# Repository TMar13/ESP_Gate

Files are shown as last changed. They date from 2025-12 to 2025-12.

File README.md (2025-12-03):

ESP Board for gate control

2 control relays (opening and partial opening)
2 24 V DC-AC  states - you can use 12V or other by adjusting R1 and R2 (10 mA optocoupler bias). It supports a dry contact imput on B3 (use 2 jumpers : see implantaion.jpg)
2 buttons for commands (opening and partial opening)
1 ESP 8266 for driving and home assistant interface

List of files:
- YAML code with two states, "open" and "closed": some gate provide the states "opening" and "closing": the code needs to be modified
- Component list and layout
- PCB files: PCB available at PCBway.fr at a competitive prices
- Electronic schematic (ignore component part numbers)
- STL Box
- Gate states flowchart

Carte de pilotage de portail à base d'ESP8266

2 relais de contrôle pour ouverture et ouverture partielle
2 états 24 V DC-AV - s'adapte à une autre tension en ajustant R1 et R2 (10 mA de polarisation de l'optocoupleur). Une entrée à contact sec est supportée sur B3 (utiliser 2 jumpers) : voir implantation.jpg
2 boutons de commande pour ouverture et ouverture partielle
1 ESP 8266 de pilotage

Liste des fichiers :
- code YAML avec 2 états "ouvert" et "fermé" : certains portails fournissent les états ouverture et fermeture : le code est à modifier
- liste des composants et implantation
- fichiers PCB : vous pouvez vous fournir chez PCBway.fr à tarif intéressant
- fichier STL pour boite
- schéma électronique (ne pas tenir compte des références des composants)
- logigramme des états du prtail

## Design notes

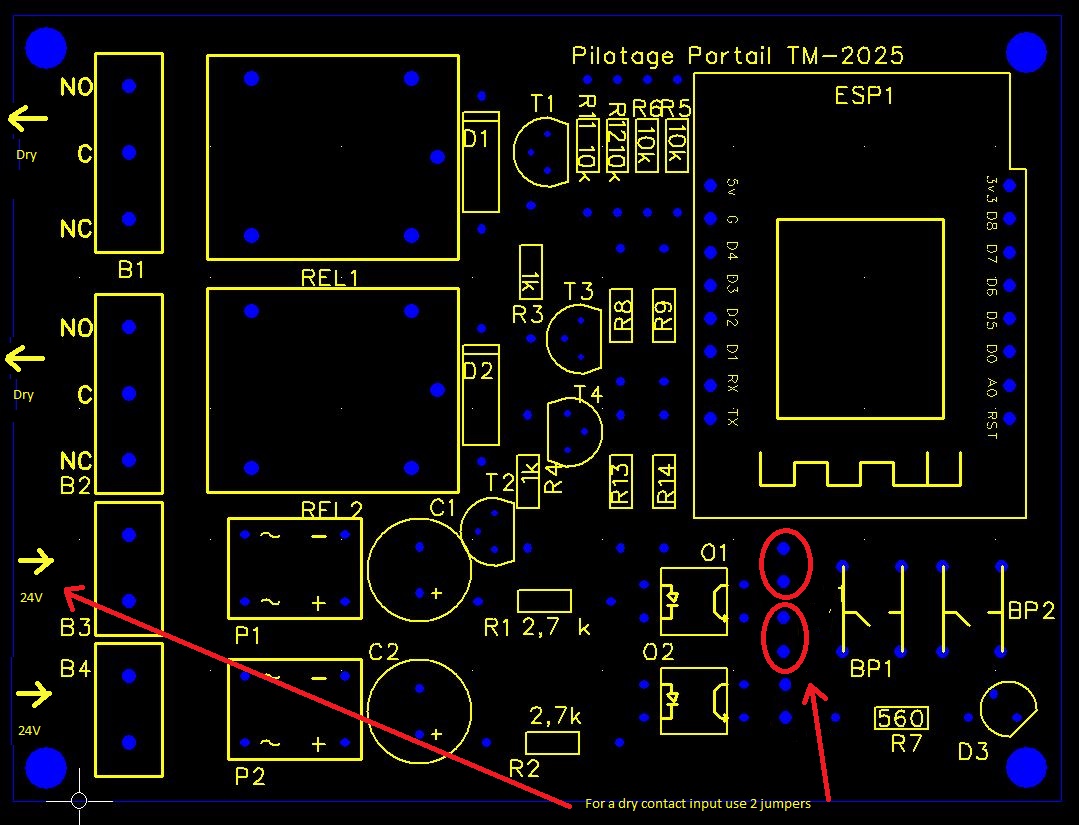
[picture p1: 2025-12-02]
implantation.JPG

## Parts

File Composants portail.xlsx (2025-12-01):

Désignation | Référence
D1,D2 | 1N4148
T1,T2 | T 58550 PNP
T3,T4 | 2N3904 NPN
ESP1 | ESP8266
R1,R2 | 2,7 kΩ
R3,R4 | 1 kΩ
R5,R6,R11,R12 | 10 kΩ
R7 | 560 Ω
R8,R9,R13,R14 | 1 kΩ
O1,O2 | Optocoupleur PC812C
P1,P2 | Pont redresseur DB207 DIP4 1000V
C1,C2 | 10 µF chimiQUE
D3 | Led 5 ou 3 mm
REL1,REL2 | Rel 5V - SRD-05VDC-SL-C
B3,B4 | Bornes doubles KF129 5,08mm
BP1, BP2 | Mini switch
B1,B21 | Bornes triples KF129 5,08mm

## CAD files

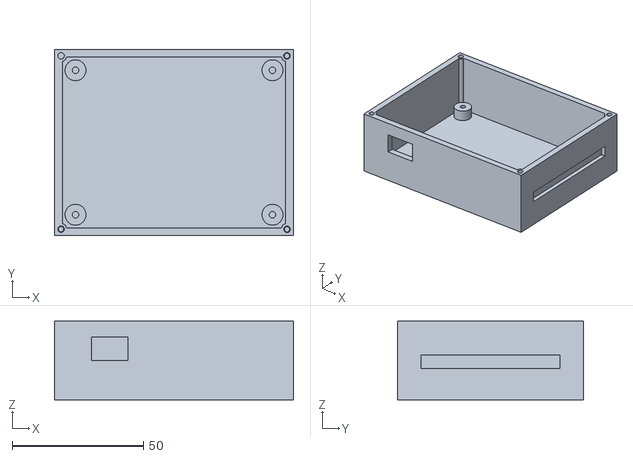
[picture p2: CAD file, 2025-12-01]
BoitePortail80x60.stl
91.0 x 71.0 x 30.0

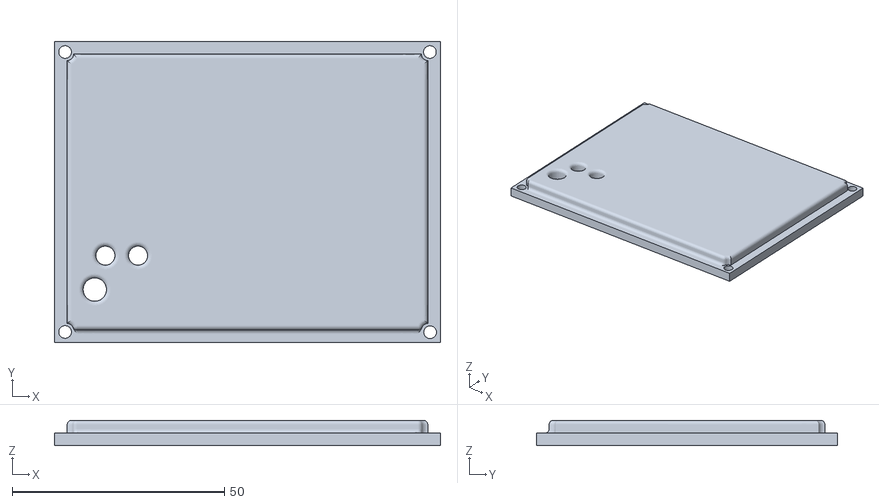
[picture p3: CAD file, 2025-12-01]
PortailCouv80x60.stl
91.0 x 71.0 x 6.00

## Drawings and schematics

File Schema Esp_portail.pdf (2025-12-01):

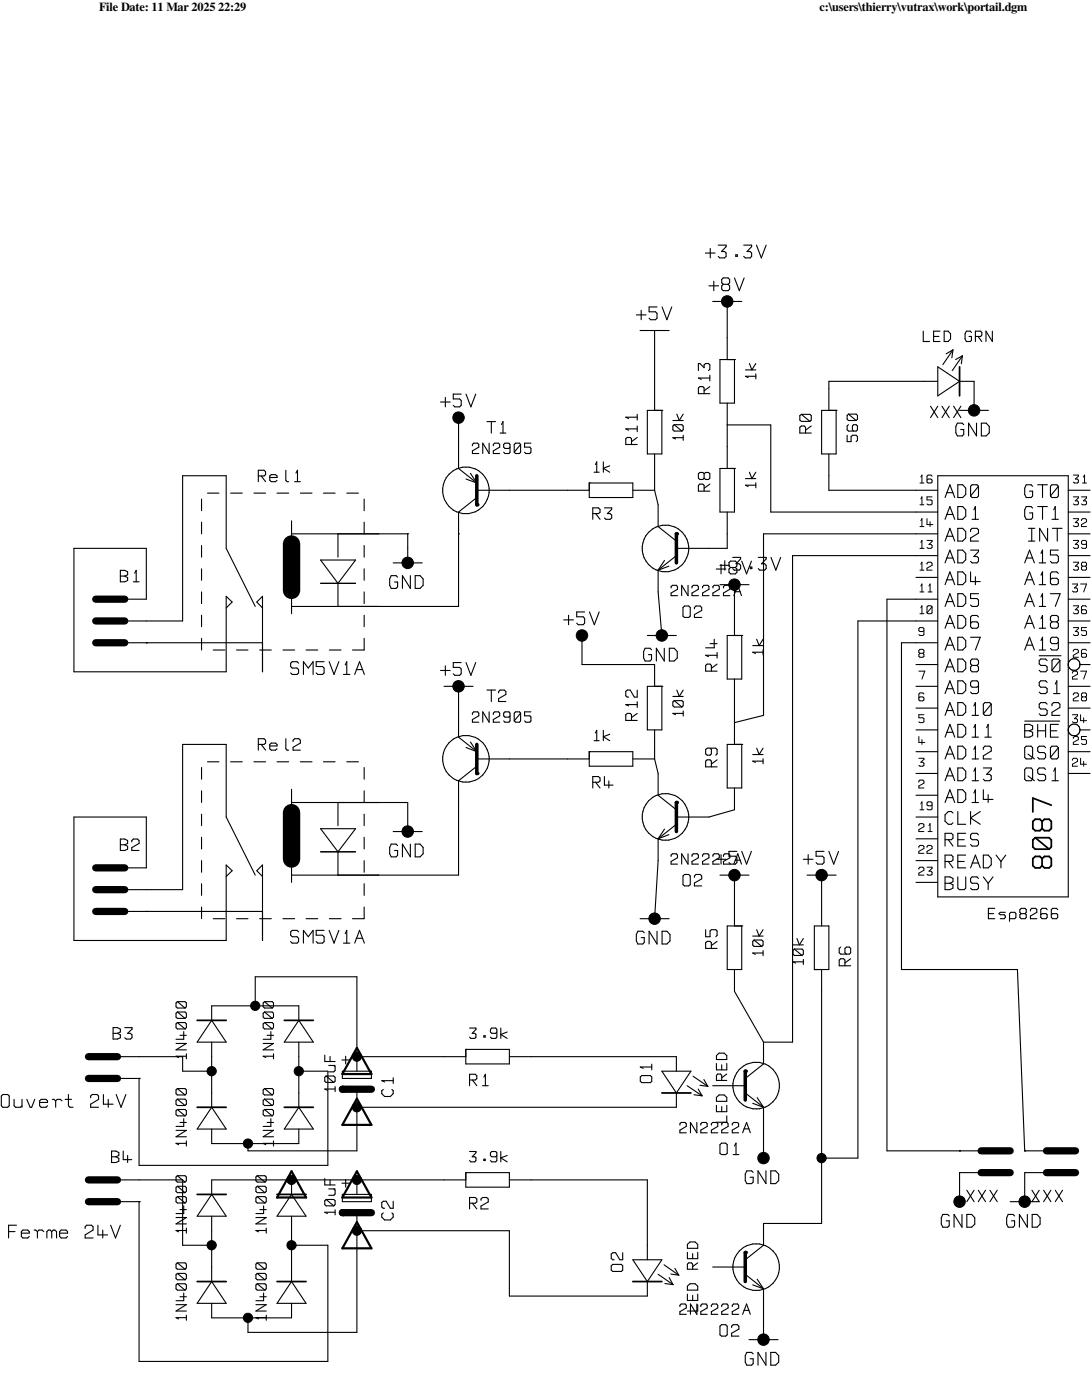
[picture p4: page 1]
File Date: 11 Mar 2025 22:29; c:\users\thierry\vutrax\work\portail.dgm

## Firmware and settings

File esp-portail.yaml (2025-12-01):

esphome:
  name: esp-portail
  friendly_name: Esp_Portail

esp8266:
  board: d1_mini

# Enable logging
logger:

# Enable Home Assistant API
api:
  encryption:
    key: "mykey"

ota:
  - platform: esphome
    password: "mypassword"

wifi:
  ssid: !secret wifi_ssid
  password: !secret wifi_password
 
  # Enable fallback hotspot (captive portal) in case wifi connection fails
  ap:
    ssid: "mon Hotspot"
    password: "mon password"

  #ptional manual IP
  manual_ip:
    static_ip: 192.168.1.xxx
    gateway: 192.168.1.1
    subnet: 255.255.255.0
  reboot_timeout: 5min

web_server:
  port: 80
  version: 3
  sorting_groups:
    - id: groupe_etats
      name: "Etats"
      sorting_weight: 10
    - id: groupe_commandes
      name: "Commandes"
      sorting_weight: 20

switch:
# Led sur la carte 
  - platform: gpio
    pin: D0
    id: led
    name: "Led Ouvert"
    restore_mode: ALWAYS_OFF
# Led ESP Bleue
  - platform: gpio
    pin: D4
    id: ledbleu
    name: "Led Bleu"
    inverted: true
# Relais de commande ouverture commande a letat 0
  - platform: gpio
    pin: D1
    id: ouvrir
    name: "Ouvrir"
    icon: "mdi:gate"
    inverted: true
    restore_mode: ALWAYS_ON
    on_turn_on:
      then:
      - delay: 500 ms
      - switch.turn_off: ouvrir
    web_server:
      sorting_group_id: groupe_commandes
# Relais de commande ouverture partielle a l'etat 0
  - platform: gpio
    pin: D2
    id: partiel
    name: "Partiel"
    icon: "mdi:gate"
    inverted: true
    restore_mode: ALWAYS_ON
    on_turn_on:
      then:
      - delay: 500 ms
      - switch.turn_off: partiel
    web_server:
      sorting_group_id: groupe_commandes
# led bleu clignotante
  - platform: template
    name: "LED Bleu lent"
    optimistic: yes
    id: bleulent
    turn_on_action:
    - while:
        condition:
          lambda: 'return true;'
        then:
        - switch.turn_on: ledbleu
        - delay: 500ms 
        - switch.turn_off: ledbleu
        - delay: 500ms
    turn_off_action:
    - switch.turn_off: ledbleu
# led bleu clignotante rapide
  - platform: template
    name: "LED Bleu rapide"
    optimistic: yes
    id: bleurapide
    turn_on_action:
    - while:
        condition:
          lambda: 'return true;'
        then:
        - switch.turn_on: ledbleu
        - delay: 200ms 
        - switch.turn_off: ledbleu
        - delay: 200ms
    turn_off_action:
    - switch.turn_off: ledbleu
# led carte clignotante
  - platform: template
    name: "LED lent"
    optimistic: yes
    id: ledlent
    turn_on_action:
    - while:
        condition:
          lambda: 'return true;'
        then:
        - switch.turn_on: led
        - delay: 500ms 
        - switch.turn_off: led
        - delay: 500ms
    turn_off_action:
    - switch.turn_off: led
# led carte clignotante rapide
  - platform: template
    name: "LED rapide"
    optimistic: yes
    id: ledrapide
    turn_on_action:
    - while:
        condition:
          lambda: 'return true;'
        then:
        - switch.turn_on: led
        - delay: 200ms 
        - switch.turn_off: led
        - delay: 200ms
    turn_off_action:
    - switch.turn_off: led
# Statud

binary_sensor:
  - platform: status
    name: "$friendly_name Status"
# Etat donne par le portail ouvert
# passe a 1 des debut ouverture
  - platform: gpio
    pin:
      number: D3
      inverted: true
      mode:
        input: true #entrée
    id: ouvert
    name: "Ouvert"
    filters:
      delayed_on_off: 1s
    on_press:
      then:
      - switch.turn_on: led
      - binary_sensor.template.publish:
          id: ouverture
          state: on
      - switch.turn_on: bleulent
    on_release:
      then:
      - switch.turn_off: led
      - binary_sensor.template.publish:
          id: fermeture
          state: off
      - switch.turn_off: bleurapide
    web_server:
      sorting_group_id: groupe_etats
#Etat ferme donne par le portail
# Passe a 0 que si totalement ouvert
  - platform: gpio
    pin:
      number: D6
      inverted: true
      mode:
        input: true #entrée
    id: ferme
    name: "Fermé"
    filters:
      delayed_on_off: 1s
    on_press:
      then:
      - switch.turn_on: bleurapide
      - binary_sensor.template.publish:
          id: fermeture
          state: on
    on_release: 
      then:
      - switch.turn_off: bleulent
      - binary_sensor.template.publish:
          id: ouverture
          state: off
    web_server:
      sorting_group_id: groupe_etats            
#Entree de bouton qui permet l'ouverture
  - platform: gpio
    pin:
      number: D5
      inverted: true # inversé : 1 quand appuyé
      mode:
        input: true #entrée
        pullup: true
    id: bouton_ouv
    name: "Bouton Ouvrir"
    filters:
      delayed_on_off: 100ms
    on_press:
      then:
      - delay: 500 ms
      - switch.turn_on: ouvrir
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
